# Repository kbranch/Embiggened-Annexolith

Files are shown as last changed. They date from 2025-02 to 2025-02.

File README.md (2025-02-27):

# Embiggened Annexolith Panels
A mod for [Esoterical](https://github.com/Esoterical)'s [Embiggened](https://github.com/Esoterical/PrinterMods/tree/main/Embiggened%20Monolith%20Panels) mod of [CloakedWayne](https://github.com/CloakedWayne)'s [Monolith panels](https://github.com/CloakedWayne/Monolith_Panels/tree/main) to include Annex-style quarter turn clips

My goal was to make the extra insulation thickness parametric, add optional heatset inserts all over the edges for mounting things, and replace the snap clips with Annex-style clips for a stronger hold to the frame. The split door from the original Monolith panels has not been converted - I would suggest a single piece door of some kind for higher temps.

Note that currently, **only the V2 is supported**. Trident support could be added if there's interest.

I have only printed the `350Bed 15.2Thick 6.6Seal 0.9Squish` version. Other combinations should work within reason, but beware of red features in the OnShape feature tree. Sanity check and test fit everything before committing to printing everything.

The source CAD is available [here on OnShape](https://cad.onshape.com/documents/7d4fb91dd4ba05e64f23a450/w/22745ee0f87958beb85178fe/e/81ea93f2c3178e66c3bc8df9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). Make your own copy to adjust the variables to match your printer.

## Instructions
### Printing
- As with the original Monolith panels, proper shrinkage compensation is critical. You'll probably be in for a bad time if you're off by even 0.1%. Be sure to average inside and outside measurements when calibrating.
- The STEP and STL files in the repo worked for my materials, but very likely will not work for you unless you buy the exact same products. I strongly suggest making your own copy of the CAD on OnShape and adjusting the variables to fit your materials. I used [1/2" PIR foam](https://www.lowes.com/pd/Johns-Manville-Common-0-5-in-x-4-ft-x-8-ft-Actual-0-5-in-x-4-ft-x-8-ft-AP-Foil-1-R-2-7-Faced-Polyisocyanurate-Foam-Board-Insulation/3851113), my stock LDO kit 3mm acrylic panels, and [1/4" D-profile silicone seals](https://www.amazon.com/dp/B0DLFV9V74?ref=ppx_yo2ov_dt_b_fed_asin_title).
- All STLs should be printed in the orientation that they come in with and without supports.
- The sides and back each use 2x`Horizontal Side`, 2x`V2 Vertical Side`, 4x`Corner`, 16x`Clip Shaft`, 16x`Clip Handle` and 16x`Clip Pin`
  - I completely deleted my exhaust port and did a full back panel, but you can probably omit the top horizontal piece to fit the stock exhaust.
  - I printed the `Clip Shaft`s with 6 walls for maximum strength, but less probably works too.
- The top is the same, except it uses 4x`Horizontal Side` and no vertical pieces.
- If you have things that you'd like to attach to the frame, insert standard Voron M3 heatset inserts where appropriate. Holes are dotted all along every piece.

### Clips
- Push a `Clip Shaft` through one of the holes, such that the part with the hole through it pokes out the side farthest from your frame. The shaft should snap into the hole once it's at the correct depth.
- Put a `Clip Handle` over the part with the hole that's poking out, such that the hole in the handle aligns with the one in the shaft. This is not designed to be a snap fit.
- Slide a `Clip Pin` through the hole in the handle with the tiny snap geometry facing away from the handle's flat side. The handle and pin should be oriented the same way that they come in in the slicer. This is designed to be a slight snap fit, and may require some force, depending on how the pieces were printed. Squeezing with needle nose pliers once the pin is started works well.
- Hold the base of the shaft against the side piece and give the clip a few rotations to wear the snap mechanism in and make sure everything fits correctly. Each 90 degree turn of the clip should take a little force and snap nicely into place at right angles.

From here, assembly is the same as the original [Monolith panels](https://github.com/CloakedWayne/Monolith_Panels/tree/main).

## CAD variables
- `TotalPanelThickness`: The total thickness of your base panel material. In my case, I used [1/2" PIR foam](https://www.lowes.com/pd/Johns-Manville-Common-0-5-in-x-4-ft-x-8-ft-Actual-0-5-in-x-4-ft-x-8-ft-AP-Foil-1-R-2-7-Faced-Polyisocyanurate-Foam-Board-Insulation/3851113) and my stock 3mm acrylic panels in a sandwich (with the acrylic on the outside, otherwise it will warp from the heat). I taped the two parts together along the edges with aluminum tape and measured the total thickness of the sandwich.
- `SealThickness`: The thickness of your sealing strip before it gets compressed. I used [1/4" D-profile silicone](https://www.amazon.com/dp/B0DLFV9V74?ref=ppx_yo2ov_dt_b_fed_asin_title). The stock foam that came with my LDO kit was absolutely unsuitable for high chamber temps.
- `SealSquish`: The amount that you want your sealing strips to get compressed after the clips are engaged. 0.9mm worked well for me.
- `BedSize`: The size of your printer's bed, e.g. 250, 300 or 350. Other sizes may work, but I did not test the CAD with them.
- `FloaterSize`: The total length of the floating piece that doesn't get attached to a corner piece. I used floaters to provide some extra pressure on edges where I had other things mounted (e.g. [Clicky-Clack](https://github.com/tanaes/whopping_Voron_mods/tree/main/clickyclacky_door) door hinges and latch)

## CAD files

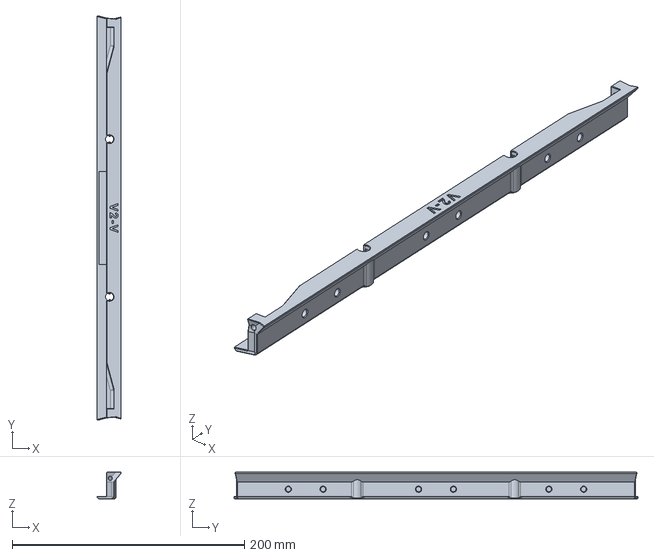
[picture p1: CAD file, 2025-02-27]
CAD/300Bed 15.2Thick 6.6Seal 0.9Squish - V2 Vertical Side.step
21.0 x 348.0 x 22.9 mm

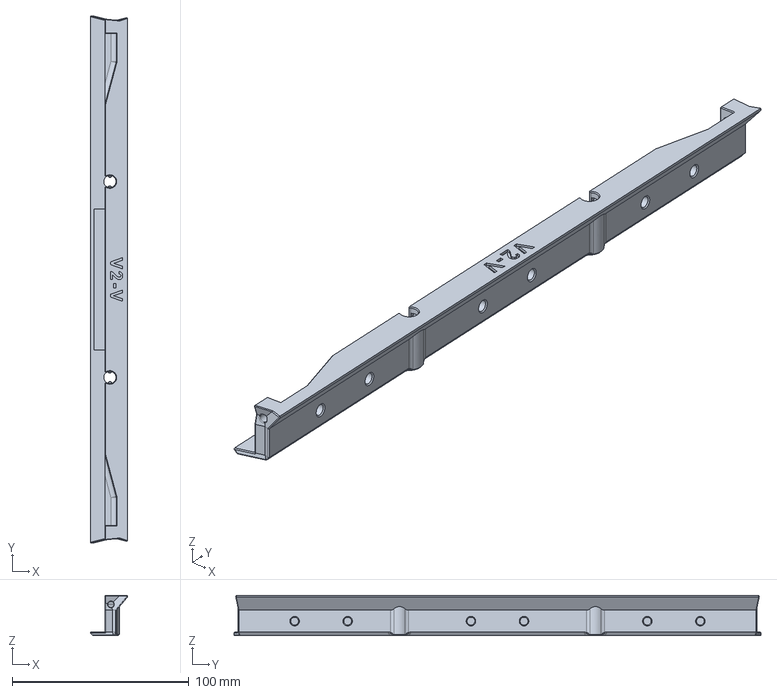
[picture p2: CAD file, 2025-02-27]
CAD/250Bed 15.2Thick 6.6Seal 0.9Squish - V2 Vertical Side.step
21.0 x 298.0 x 22.9 mm

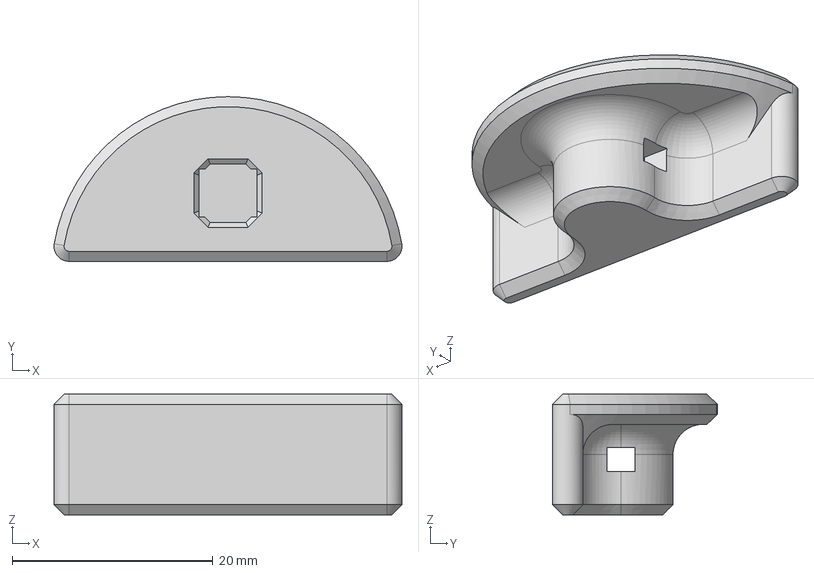
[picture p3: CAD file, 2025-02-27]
CAD/All - Clip Handle.step
34.6 x 16.4 x 12.0 mm

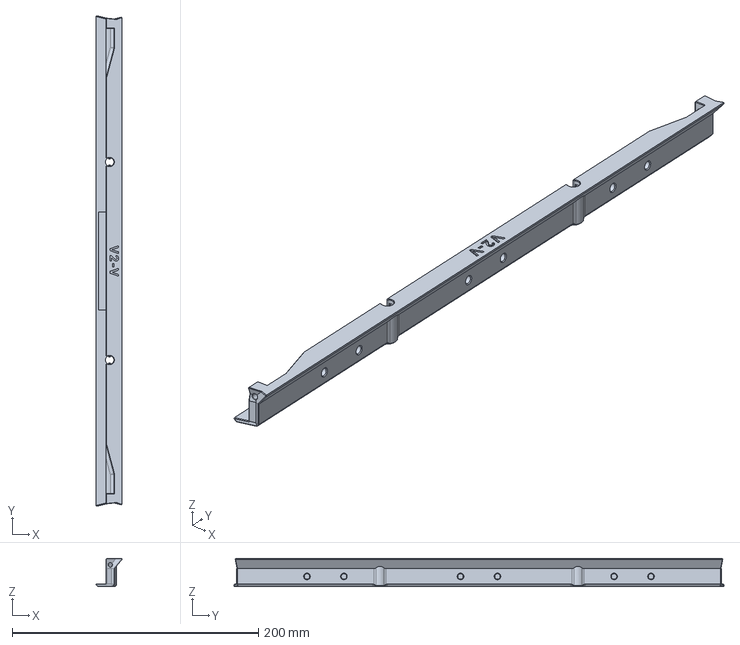
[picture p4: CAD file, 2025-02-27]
CAD/350Bed 15.2Thick 6.6Seal 0.9Squish - V2 Vertical Side.step
21.0 x 398.0 x 22.9 mm

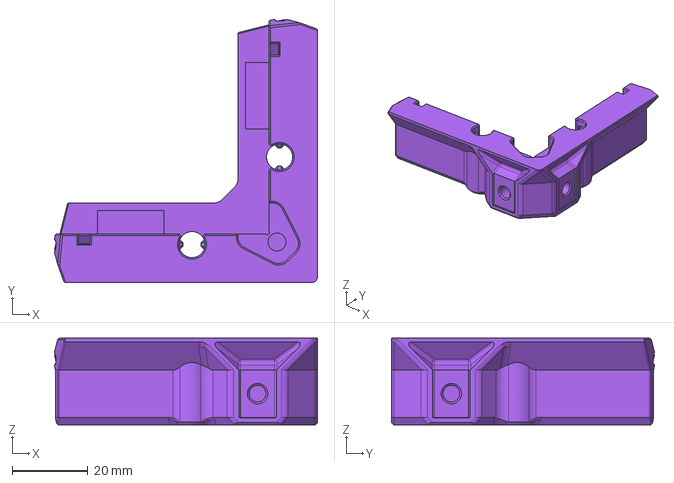
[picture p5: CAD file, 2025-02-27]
CAD/AllBed 15.2Thick 6.6Seal 0.9Squish - Corner.step
69.4 x 69.4 x 22.9 mm

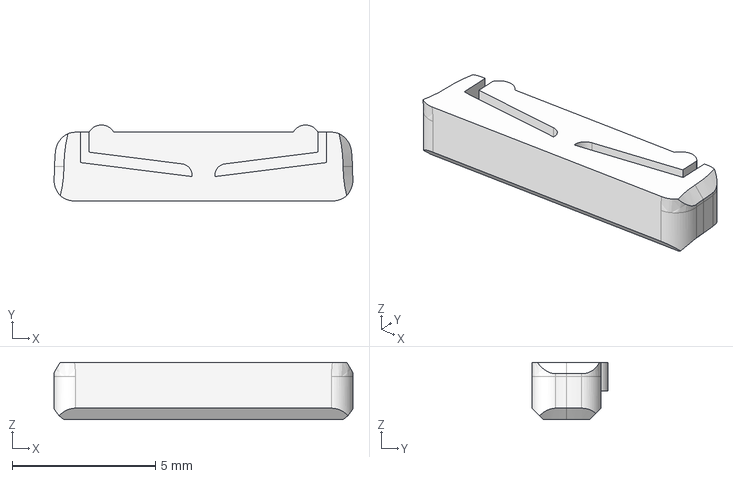
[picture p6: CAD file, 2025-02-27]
CAD/All - Clip Pin.step
10.4 x 2.65 x 2.00 mm

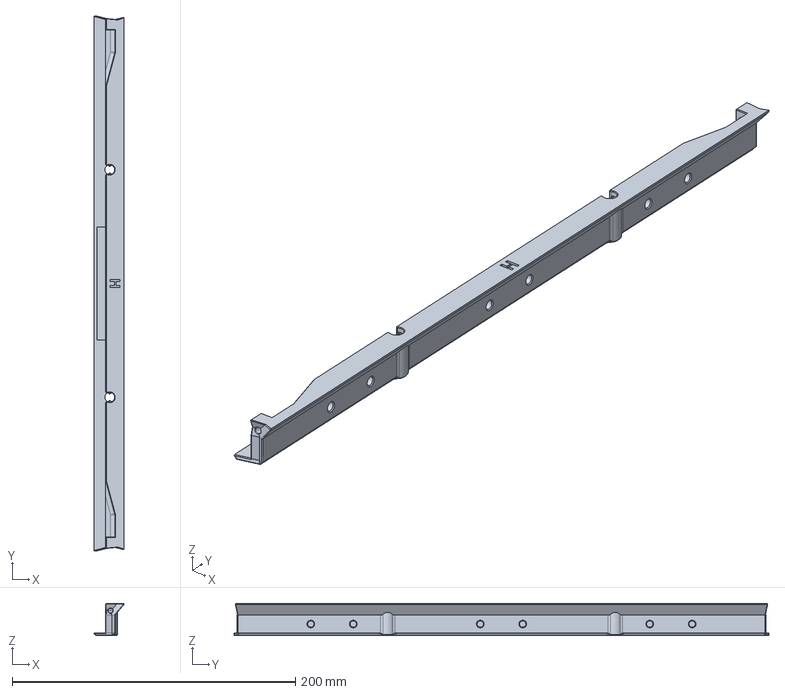
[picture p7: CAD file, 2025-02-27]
CAD/350Bed 15.2Thick 6.6Seal 0.9Squish - Horizontal Side.step
21.0 x 378.0 x 22.9 mm

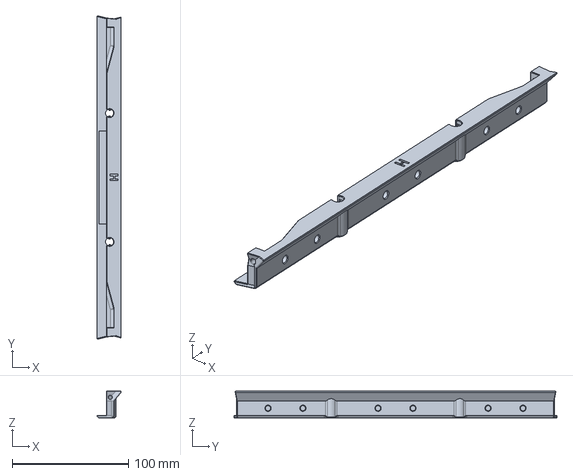
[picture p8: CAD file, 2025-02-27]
CAD/250Bed 15.2Thick 6.6Seal 0.9Squish - Horizontal Side.step
21.0 x 278.0 x 22.9 mm

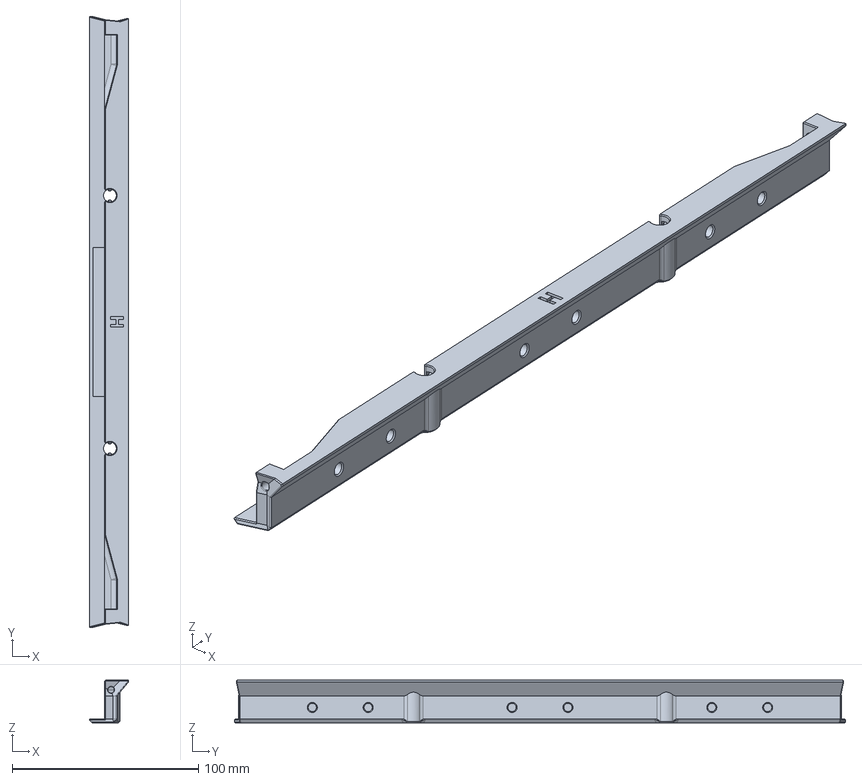
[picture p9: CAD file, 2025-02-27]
CAD/300Bed 15.2Thick 6.6Seal 0.9Squish - Horizontal Side.step
21.0 x 328.0 x 22.9 mm

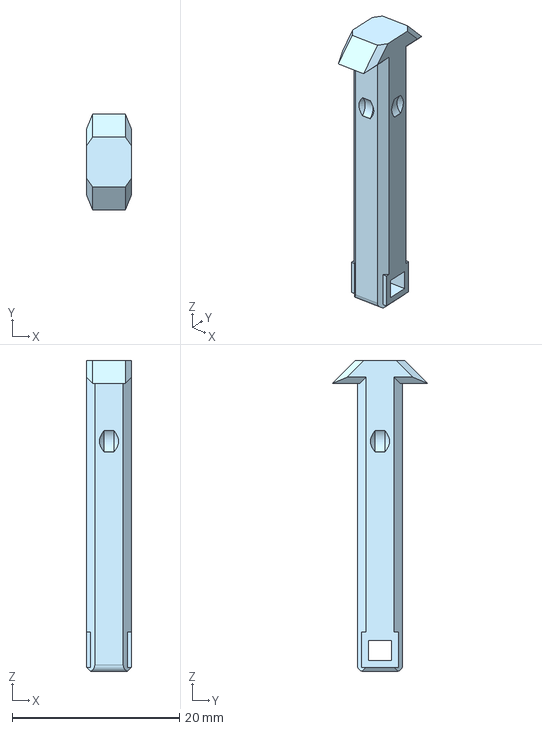
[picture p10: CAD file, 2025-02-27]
CAD/AllBed 15.2Thick 6.6Seal 0.9Squish - Clip Shaft.step
5.40 x 11.5 x 37.1 mm

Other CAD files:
STLs/250Bed 15.2Thick 6.6Seal 0.9Squish - Horizontal Side.stl
STLs/250Bed 15.2Thick 6.6Seal 0.9Squish - V2 Vertical Side.stl
STLs/300Bed 15.2Thick 6.6Seal 0.9Squish - Horizontal Side.stl
STLs/300Bed 15.2Thick 6.6Seal 0.9Squish - V2 Vertical Side.stl
STLs/350Bed 15.2Thick 6.6Seal 0.9Squish - Horizontal Side.stl
STLs/350Bed 15.2Thick 6.6Seal 0.9Squish - V2 Vertical Side.stl
STLs/All - Clip Handle.stl
STLs/All - Clip Pin.stl
STLs/AllBed 15.2Thick 6.6Seal 0.9Squish - Clip Shaft.stl
STLs/AllBed 15.2Thick 6.6Seal 0.9Squish - Corner.stl
